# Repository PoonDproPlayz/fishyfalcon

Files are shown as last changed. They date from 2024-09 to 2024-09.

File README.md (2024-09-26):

# FishyFalcon
A quad motor 3D printer board that supports spi or uart control on stepstick drivers and external driver functionality it is based around the STM32 Blackpill and the Pi Pico.<br />
### Features
&nbsp;&nbsp;&nbsp;&nbsp;&nbsp;&nbsp;&nbsp;&nbsp;• SPI or UART on all 4 motors<br/>
&nbsp;&nbsp;&nbsp;&nbsp;&nbsp;&nbsp;&nbsp;&nbsp;• External driver support through the AO3400 mosfet<br/>
&nbsp;&nbsp;&nbsp;&nbsp;&nbsp;&nbsp;&nbsp;&nbsp;• Dual driver control through only 3 pins<br/>
&nbsp;&nbsp;&nbsp;&nbsp;&nbsp;&nbsp;&nbsp;&nbsp;• Sensorless homing (not tested yet)
# Bill Of Materials
| Component Name  | No. Required | Total Price | Remarks | Link |
| --- | --- | --- | --- | --- |
| 7.62mm Screw Terminal 4P | 1 | $ 0.2115 | Power in | [https://www.lcsc.com/product-detail/Barrier-Terminal-Blocks_Cixi-Kefa-Elec-KF7-62-4P_C707826.html](https://www.lcsc.com/product-detail/Barrier-Terminal-Blocks_Cixi-Kefa-Elec-KF7-62-4P_C707826.html) |
| 0.2uF SMD capacitor | 4 | $ 0.54 | C0805 | [https://www.lcsc.com/product-detail/Multilayer-Ceramic-Capacitors-MLCC-SMD-SMT_CCTC-TCC0805X7R204K500DT_C344170.html](https://www.lcsc.com/product-detail/Multilayer-Ceramic-Capacitors-MLCC-SMD-SMT_CCTC-TCC0805X7R204K500DT_C344170.html) |
| 2x3 2.54mm male pins | 4 | $ 0.44 | Diag configuration | [https://www.lcsc.com/product-detail/Pin-Headers_CJT-Changjiang-Connectors-A2541WV-2x3P_C225518.html](https://www.lcsc.com/product-detail/Pin-Headers_CJT-Changjiang-Connectors-A2541WV-2x3P_C225518.html) |
| 3x3 2.54mm male pins | 4 | $ 0.88 | SPI/UART configuration | [https://www.lcsc.com/product-detail/Pin-Headers_HCTL-PZ254-3-03-Z-2-5-G0_C7429377.html](https://www.lcsc.com/product-detail/Pin-Headers_HCTL-PZ254-3-03-Z-2-5-G0_C7429377.html) |
| JST XH 2P | 4 | $ 0.36 | Endstops | [https://www.lcsc.com/product-detail/Wire-To-Board-Connector_span-style-background-color-ff0-JST-span-B2B-XH-A-LF-SN_C158012.html](https://www.lcsc.com/product-detail/Wire-To-Board-Connector_span-style-background-color-ff0-JST-span-B2B-XH-A-LF-SN_C158012.html) |
| JST XH 4P | 4 | $ 0.42 | Driver out | [https://www.lcsc.com/product-detail/Wire-To-Board-Connector_span-style-background-color-ff0-JST-span-B4B-XH-A-LF-SN_C144395.html](https://www.lcsc.com/product-detail/Wire-To-Board-Connector_span-style-background-color-ff0-JST-span-B4B-XH-A-LF-SN_C144395.html) |
| AO3400A | 12 | $ 1.07 | SOT-23 Mosfet for external driver | [https://www.lcsc.com/product-detail/MOSFETs_Alpha-Omega-Semicon-AO3400A_C20917.html](https://www.lcsc.com/product-detail/MOSFETs_Alpha-Omega-Semicon-AO3400A_C20917.html) |
| 10K SMD Resistor | 4 | $ 0.22 | R1206 1/4W Enable pin resistor | [https://www.lcsc.com/product-detail/Chip-Resistor-Surface-Mount_FH-Guangdong-Fenghua-Advanced-Tech-RS-06K103JT_C118075.html](https://www.lcsc.com/product-detail/Chip-Resistor-Surface-Mount_FH-Guangdong-Fenghua-Advanced-Tech-RS-06K103JT_C118075.html) |
| 0Ω SMD Resistor | 12 | $ 0.39 | R1206 Check if your mosfet needs a differnt value resistor | [https://www.lcsc.com/product-detail/Chip-Resistor-Surface-Mount_Vishay-Intertech-RCA12060000ZSEA_C4126934.html](https://www.lcsc.com/product-detail/Chip-Resistor-Surface-Mount_Vishay-Intertech-RCA12060000ZSEA_C4126934.html) |
| JST XH 6P | 4 | $ 0.65 | External driver out | [https://www.lcsc.com/product-detail/Wire-To-Board-Connector_span-style-background-color-ff0-JST-span-B6B-XH-AM-LF-SN_C161873.html](https://www.lcsc.com/product-detail/Wire-To-Board-Connector_span-style-background-color-ff0-JST-span-B6B-XH-AM-LF-SN_C161873.html) |
| 63v 330 or 470uF electrolytic cap | 4 | $ 1.71 | Stepper caps | [https://www.lcsc.com/product-detail/Aluminum-Electrolytic-Capacitors-Leaded_SamYoung-Electronics-NXA63V470M12-5-20-5-0TP_C346981.html](https://www.lcsc.com/product-detail/Aluminum-Electrolytic-Capacitors-Leaded_SamYoung-Electronics-NXA63V470M12-5-20-5-0TP_C346981.html) |
| 10A ATO fuse | 2 | $ 0.45 | Power in fuse | [Aliexpress](https://aliexpress.com/item/1005005797789486.html)  [LCSC](https://www.lcsc.com/product-detail/Fuse-Holders_XFCN-XF-506P_C492610.html) |
| 1x20 2.54 female pins | 2-4 | $ 0.76 | Blackpill/pico socket | [https://www.lcsc.com/product-detail/Female-Headers_JILN-22850120ANG1SYA01_C429947.html](https://www.lcsc.com/product-detail/Female-Headers_JILN-22850120ANG1SYA01_C429947.html) |
| 1x8 2.54 female pins | 8 | $ 0.53 | Stepstick socket | [https://www.lcsc.com/product-detail/Female-Headers_Liansheng-FH-00882_C2685213.html](https://www.lcsc.com/product-detail/Female-Headers_Liansheng-FH-00882_C2685213.html) |
| 1x3 2.54 male pins | 10 | $ 1.52 | Dual driver and motor voltage selection | [https://www.lcsc.com/product-detail/Wire-To-Board-Connector_MOLEX-22032031_C505002.html](https://www.lcsc.com/product-detail/Wire-To-Board-Connector_MOLEX-22032031_C505002.html) |
| 1x2 2.54 male pins | 4 | $ 0.60 | Diag and vref pins | [https://www.lcsc.com/product-detail/span-style-background-color-ff0-Female-span-Headers_Shenzhen-Kinghelm-Elec-KH-2-54FH-1X2P-H8-5_C2905414.html](https://www.lcsc.com/product-detail/span-style-background-color-ff0-Female-span-Headers_Shenzhen-Kinghelm-Elec-KH-2-54FH-1X2P-H8-5_C2905414.html)|
| STM32F4x1 Blackpill | 1 | $ 3.05 | MCU(Choose one) | [https://www.aliexpress.com/item/1005006127461676.html](https://www.aliexpress.com/item/1005006127461676.html) |
| Pi Pico | 1 | $ 2.66 | MCU(Choose one) | [https://th.aliexpress.com/item/1005003708090298.html?gatewayAdapt=glo2tha](https://aliexpress.com/item/1005003708090298.html) |
| MC34063ADR | 1 | $ 1.30 | SOIC-8 Adjustable dc-dc converter | [https://www.lcsc.com/product-detail/DC-DC-Converters_Texas-Instruments-MC34063ADR_C100023.html](https://www.lcsc.com/product-detail/DC-DC-Converters_Texas-Instruments-MC34063ADR_C100023.html) |
| 0.33Ω SMD Resistor | 1 | $ 0.29 | 0603 resistor | [https://www.lcsc.com/product-detail/Chip-Resistor-Surface-Mount_UNI-ROYAL-Uniroyal-Elec-0603WAJ033KT5E_C247018.html](https://www.lcsc.com/product-detail/Chip-Resistor-Surface-Mount_UNI-ROYAL-Uniroyal-Elec-0603WAJ033KT5E_C247018.html) |
| 470pf SMD Cap | 1 | $ 0.26 | 0603 Cap | [https://www.lcsc.com/product-detail/Multilayer-Ceramic-Capacitors-MLCC-SMD-SMT_FH-Guangdong-Fenghua-Advanced-Tech-0603B471K500NT_C1620.html](https://www.lcsc.com/product-detail/Multilayer-Ceramic-Capacitors-MLCC-SMD-SMT_FH-Guangdong-Fenghua-Advanced-Tech-0603B471K500NT_C1620.html) |
| 1N5819 Diode | 1 | $ 0.42 | Schottkey Diode | [https://www.lcsc.com/product-detail/Schottky-Diodes_STMicroelectronics-1N5819_C110032.html](https://www.lcsc.com/product-detail/Schottky-Diodes_STMicroelectronics-1N5819_C110032.html) |
| 220uH SMD inductor | 1 | $ 0.41 | SMD inductor | [https://www.lcsc.com/product-detail/Power-Inductors_YJYCOIN-CD54YP0504-221M_C492674.html](https://www.lcsc.com/product-detail/Power-Inductors_YJYCOIN-CD54YP0504-221M_C492674.html) |
| 1uH SMD inductor | 1 | $ 0.19 | L0603 inductor | [https://www.lcsc.com/product-detail/Inductors-SMD_Sunlord-SDFL1608Q1R0KTF_C22037.html](https://www.lcsc.com/product-detail/Inductors-SMD_Sunlord-SDFL1608Q1R0KTF_C22037.html) |
| 3.83K SMD resistor | 1 | $ 0.10 | 0603 resistor | [https://www.lcsc.com/product-detail/Chip-Resistor-Surface-Mount_UNI-ROYAL-Uniroyal-Elec-0603WAF3831T5E_C22982.html](https://www.lcsc.com/product-detail/Chip-Resistor-Surface-Mount_UNI-ROYAL-Uniroyal-Elec-0603WAF3831T5E_C22982.html) |
| 100uf 63v cap | 2 | $ 0.53 | 100uf tht cap | [https://www.lcsc.com/product-detail/Aluminum-Electrolytic-Capacitors-Leaded_CX-Dongguan-Chengxing-Elec-KM107M063G13RR0VH2FP0_C45675.html](https://www.lcsc.com/product-detail/Aluminum-Electrolytic-Capacitors-Leaded_CX-Dongguan-Chengxing-Elec-KM107M063G13RR0VH2FP0_C45675.html) |
| 470uf 50v cap | 1 | $ 0.54 | 470uf tht cap | [https://www.lcsc.com/product-detail/Aluminum-Electrolytic-Capacitors-Leaded_CX-Dongguan-Chengxing-Elec-GR477V050G20RR0VH4FP0_C3312.html](https://www.lcsc.com/product-detail/Aluminum-Electrolytic-Capacitors-Leaded_CX-Dongguan-Chengxing-Elec-GR477V050G20RR0VH4FP0_C3312.html) |
| 1.2k SMD resistor  | 1 | $ 0.66 | 0603 SMD resistor | [https://www.lcsc.com/product-detail/Chip-Resistor-Surface-Mount_Viking-Tech-AR03DTCX1201_C319998.html](https://www.lcsc.com/product-detail/Chip-Resistor-Surface-Mount_Viking-Tech-AR03DTCX1201_C319998.html) |

Total(Excluding shipping/tax etc.) ≈ $ 12.8

# Dual Driver Setting
| Setting | Instructions |
| --- | --- |
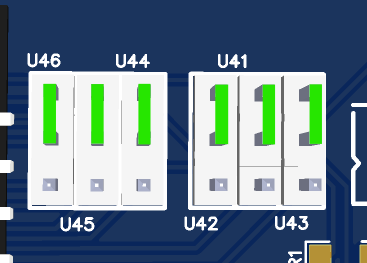
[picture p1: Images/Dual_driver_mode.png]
dual driver mode
| |Bridge the following pins with jumpers to drive driver 1 and 2 together and driver 3 and 4 together |
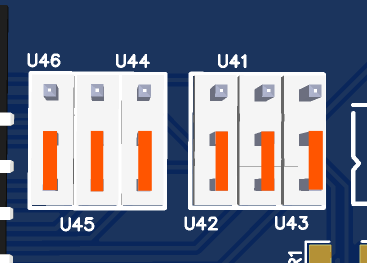
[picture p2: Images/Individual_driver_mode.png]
Single driver mode
| |Bridge the following pins with jumpers to individually drive each motor |

Left side is driver 1 and 2 right is 3 and 4. Each 3x3 block has DIR, STEP, EN in order from left to right

# Motor Voltage Selection

| Setting | Instructions |
| --- | --- |
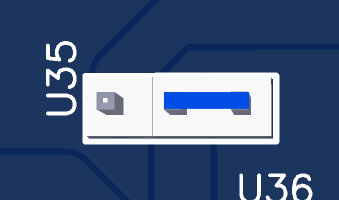
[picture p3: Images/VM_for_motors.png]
|| Bridge the following pins with jumpers to supply the motor with the VM DC input |
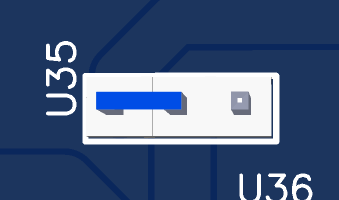
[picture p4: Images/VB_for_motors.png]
|| Bridge the following pins with jumpers to supply the motor with the VB DC input |

# Assembly
[PCB Assembly](https://github.com/PoonDproPlayz/fishyfalcon/blob/main/Docs/Assembly.md)<br />
[Board Mounting](https://github.com/PoonDproPlayz/fishyfalcon/blob/main/Docs/Mounting%20the%20board.md)

# Credits
&nbsp;&nbsp;&nbsp;&nbsp;&nbsp;&nbsp;&nbsp;&nbsp;• **69420exp** For his work on Dual driver control and part of the schematics<br />
&nbsp;&nbsp;&nbsp;&nbsp;&nbsp;&nbsp;&nbsp;&nbsp;• **Annex Engineering** For their pinouts<br />
&nbsp;&nbsp;&nbsp;&nbsp;&nbsp;&nbsp;&nbsp;&nbsp;• **comradef191** (Discord:f191) For the jumper configurations for the stepstick/polulu style drivers and the extensive work on the CAD models<br />

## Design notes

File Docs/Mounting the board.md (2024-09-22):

# Mounting the board
| Instructions | Image |
| --- | --- |
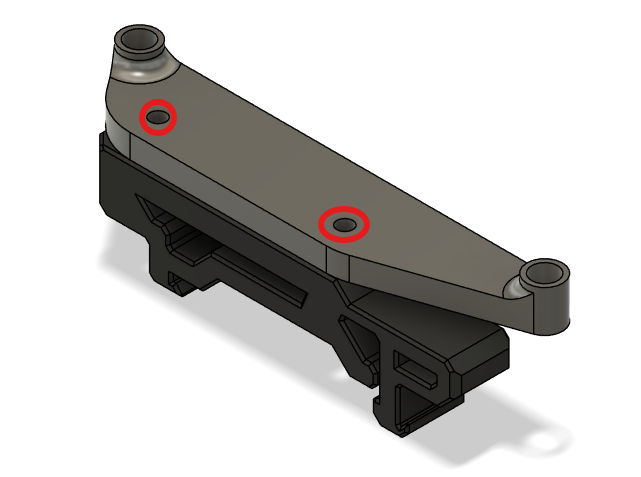
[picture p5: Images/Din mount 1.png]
Board mount 1
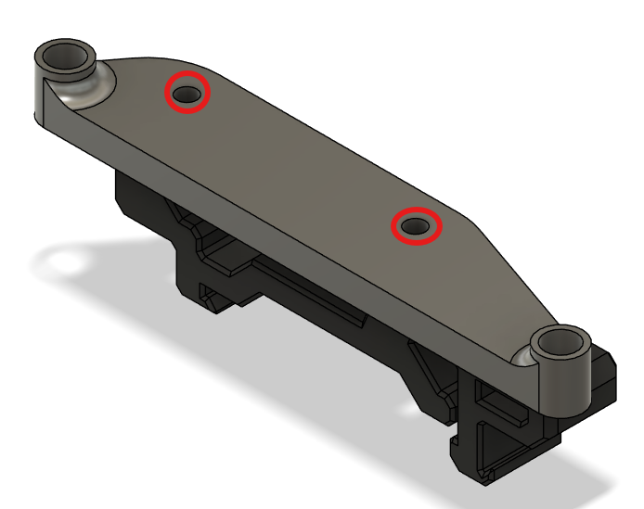
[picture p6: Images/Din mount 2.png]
Board mount 2
| Install M3x4x5 Heatset inserts into the circled areas and repeat for the other side |   |
| Screw in an M2x10 self tapping into the circled areas to attach the din rail mount and the board mount repeat for the other side| Din mount 1 Din mount 2 |
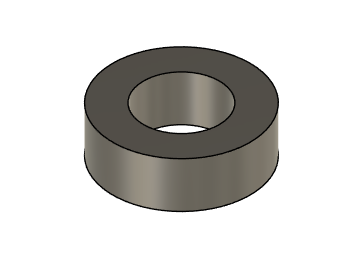
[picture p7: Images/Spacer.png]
Spacer
| Place the board on top of the board mounts and use a M3x8 SHCS to tighten the board down to the board mount making sure to place the spacer on to of the board first |  |

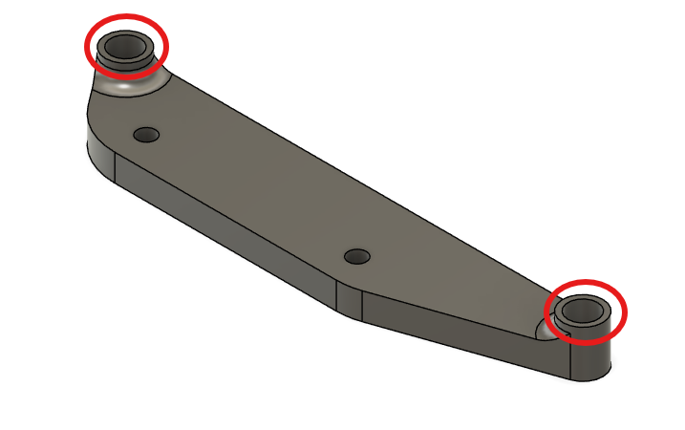
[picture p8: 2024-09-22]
Images/Board mount 1.png

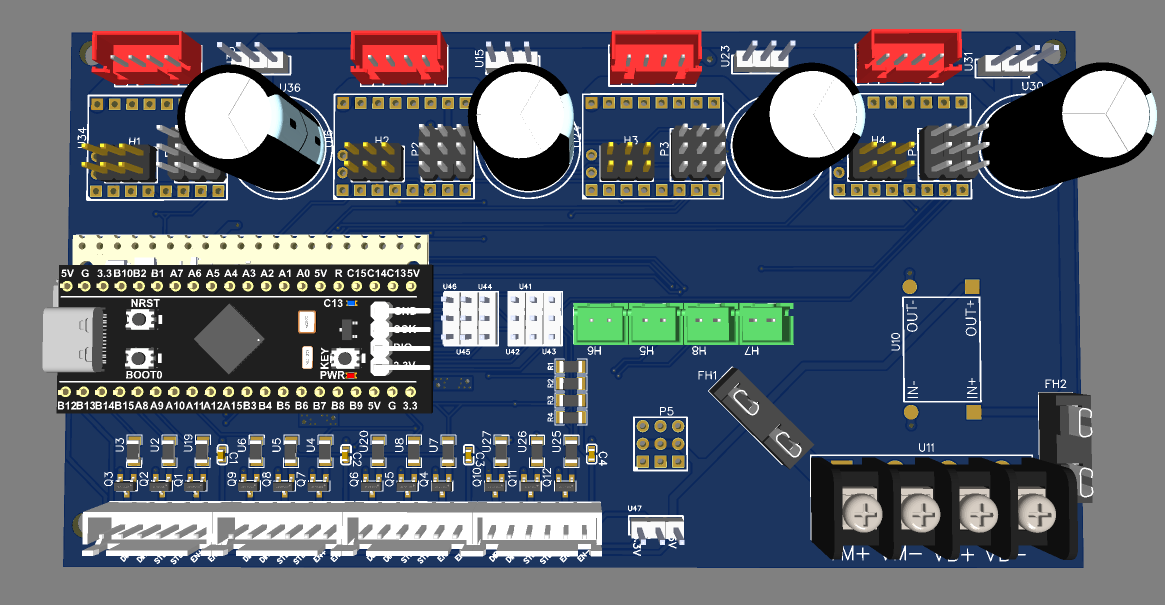
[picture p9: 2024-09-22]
Images/Full board.png

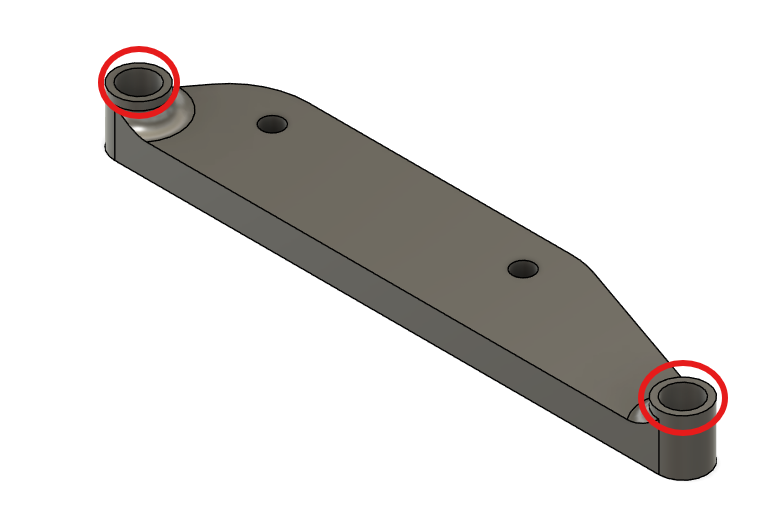
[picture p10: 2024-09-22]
Images/Board mount 2.png

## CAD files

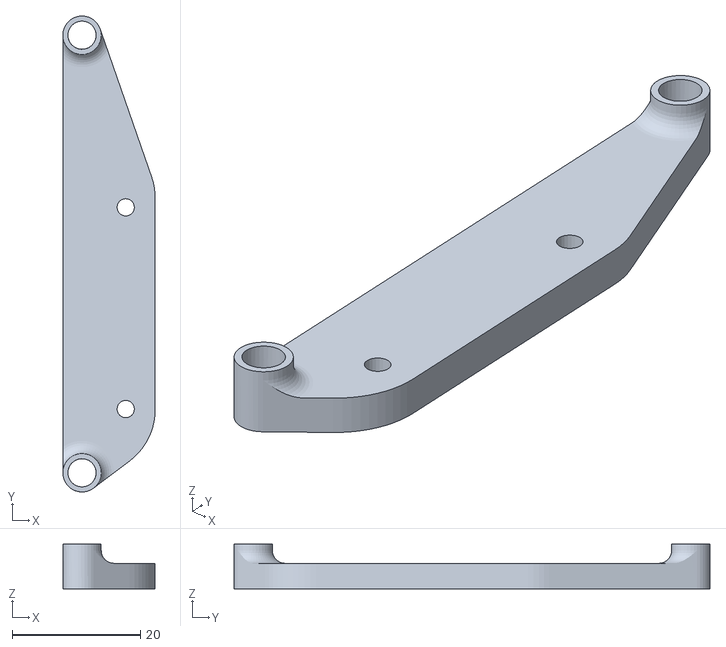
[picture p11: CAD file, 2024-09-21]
STLs/Board mount left.stl
14.4 x 74.3 x 7.00

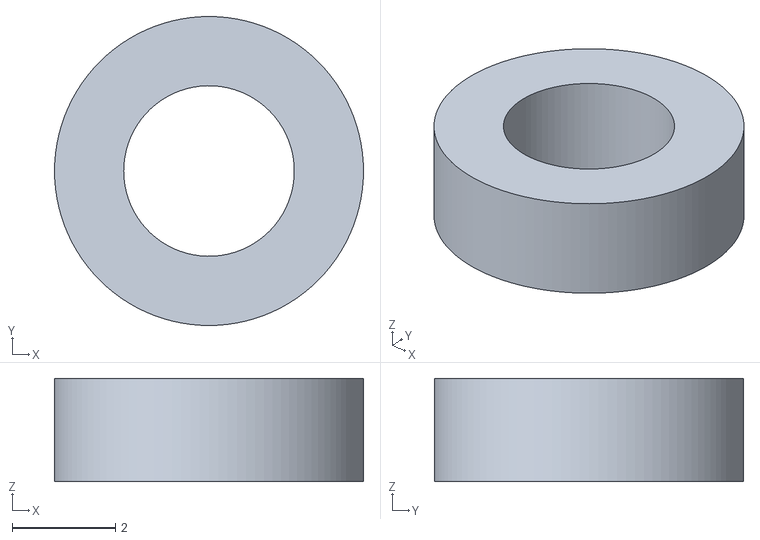
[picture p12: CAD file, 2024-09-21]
STLs/Board spacer x4.stl
6.00 x 6.00 x 2.00

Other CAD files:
STLs/Board mount right.stl

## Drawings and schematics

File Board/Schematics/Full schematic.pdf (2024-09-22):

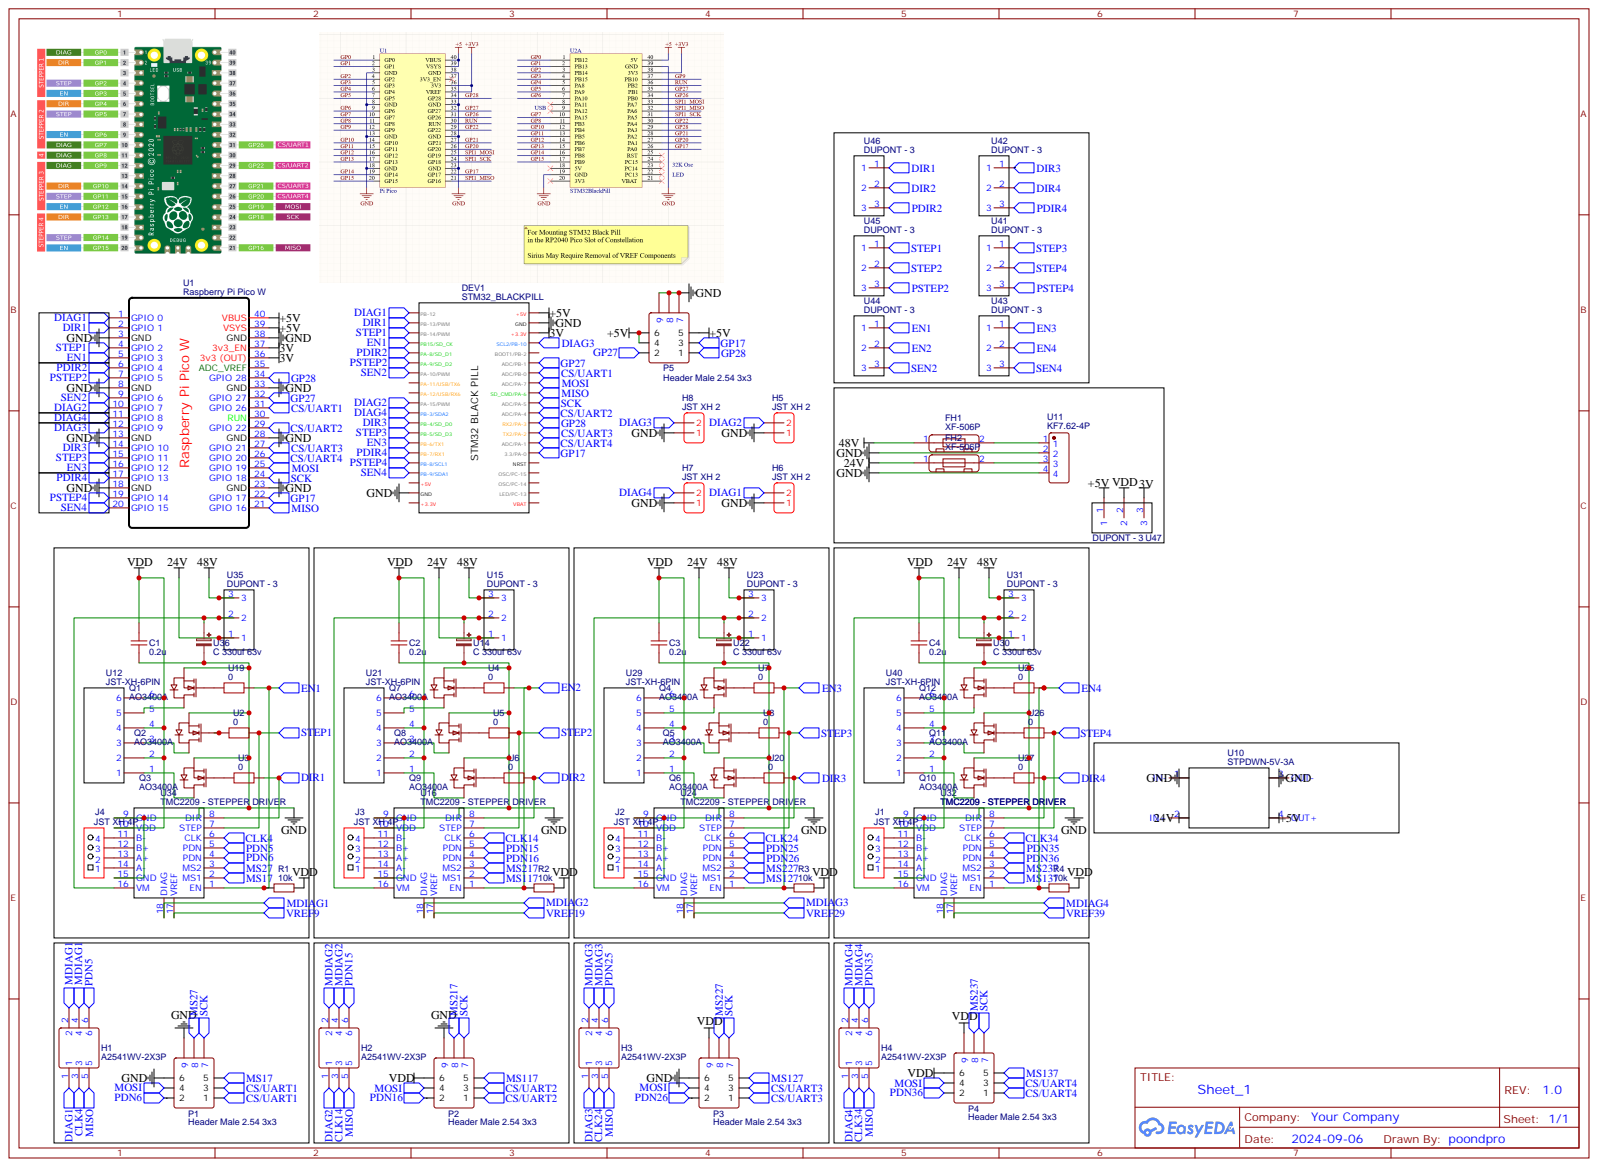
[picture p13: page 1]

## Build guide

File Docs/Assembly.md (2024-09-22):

# Assembling the board
| Notes | Images |
| --- | --- |
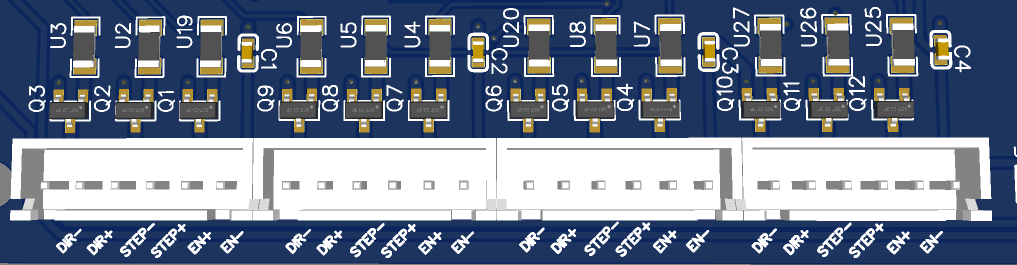
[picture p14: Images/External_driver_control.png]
external_driver
| AO3400 mosfets go on prefixes begining with Q. 0Ω R1206 resistors go on prefixes begining with U and 0.2uf C0603 caps go on prefixes begining with C. JST XH goes at the bottom row.|  |
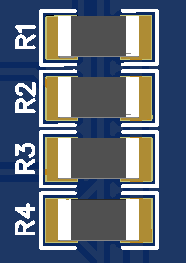
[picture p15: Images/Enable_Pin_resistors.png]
enables resistors
| 10K R1206 go on prefixes beginning with R |  |
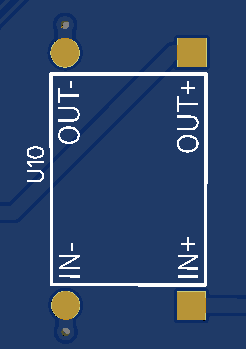
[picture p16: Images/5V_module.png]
5v module
| 5V converter module is soldered on here (Make sure your orientation is correct!)|  |
| 6 1x3 male dupont pin headers go on the prefixes begining with U. JST XH 2P go on prefixes begining with H | Endstop and dual driver |
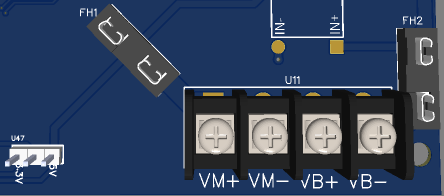
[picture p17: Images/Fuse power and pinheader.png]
Fuse and power in
| Fuses and wire terminals get soldered on into its corresponding slots |  |
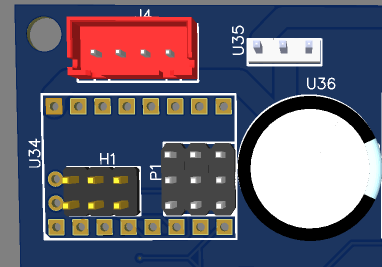
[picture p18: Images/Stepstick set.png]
Stepstick slot
| The 330 or 470uf caps go into its slot between the drivers (Make sure your orientation is correct!). Female 1x8 and 1x2 dupont pin headers go on the stepstick slot. 2x3 and 3x3 male pinheaders go between the stepstick pinheaders. JST XH 4P and 1x3 male dupont headers go at the top |  |

[Mounting the board](https://github.com/PoonDproPlayz/fishyfalcon/blob/main/Docs/Mounting%20the%20board.md)

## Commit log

2024-09-21 Added stls
    [Board mount left.stl, Board mount right.stl, Board spacer x4.stl]
2024-09-22 updates assembly.md and readme.md
2024-09-22 added mounting the board
2024-09-22 added mount images
2024-09-22 Update Din mount 2.png
2024-09-22 Update Mounting the board.md
2024-09-22 Added pcb files
2024-09-22 updated pcb
2024-09-22 Added some 3d models and schematics
